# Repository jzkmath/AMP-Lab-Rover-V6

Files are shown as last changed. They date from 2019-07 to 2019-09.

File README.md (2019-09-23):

# AMP-Lab-Rover-V6
Low Cost Rover V6 Design Files.

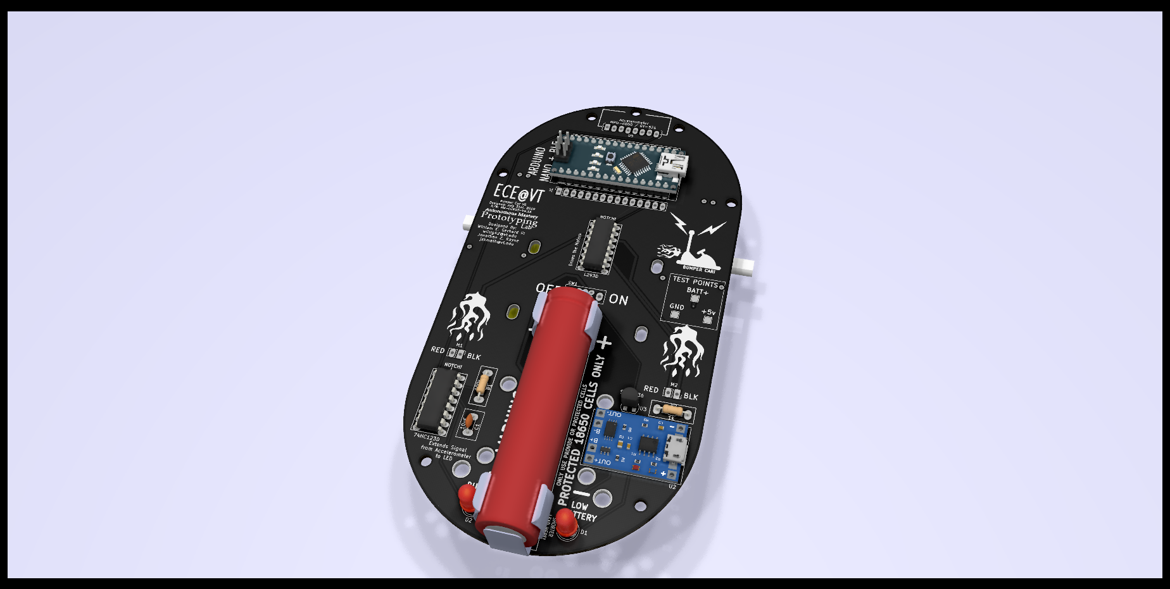
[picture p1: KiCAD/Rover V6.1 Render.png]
render1


This uses a Arduino Nano with Bluetooth Low Energy Module built-in to communicate with a smartphone through the Blynk App.

You will need to download the Blynk library to get the sketch to compile.

## Assembly Instructions

Video Tutorial: https://www.youtube.com/playlist?list=PL4FFrmT3l_b0y4ERLvnKdsL8f40yGXgXS

Written Manual: TBA

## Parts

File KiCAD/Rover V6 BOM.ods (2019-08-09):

Item | Qty | Reference(s) | Description | McMaster Carr PN | Amazon PN | Digikey PN | Link | Unit Cost | Total Cost
1 | 1 | A1 | Arduino Nano + BLE |  | B07QM6KHS4 |  | https://amzn.com/B07QM6KHS4 | $10.99 | $10.99
2 | 2 | BT1 | Battery Clip, Keystone 54 |  |  | 36-54-ND | https://www.digikey.com/short/p9dctd | $0.57 | $1.14
3 | 1 | C1 | 10uF Capacitor |  |  | 445-8396-ND | https://www.digikey.com/short/p9dc35 | $0.40 | $0.40
4 | 1 | D1 | LED |  |  | C5SMF-RJF-CT0W0BB1-ND | https://www.digikey.com/short/p9dc3v | $0.14 | $0.14
5 | 1 | D2 | RGB LED |  | B01C19ENG4 |  | https://amzn.com/B01C19ENG4 | $0.0698 | $0.07
6 | 2 | M1, M2 | Arduino DC Gearbox Motor |  | B07DQGX369 |  | https://amzn.com/B07DQGX369 | $3.75 | $7.50
7 | 1 | R2 | 1k Resistor |  |  | CF18JT1K00CT-ND | https://www.digikey.com/short/p9dcq3 | $0.10 | $0.10
8 | 1 | R1 | 100k Resistor |  |  | CF18JT100KCT-ND | https://www.digikey.com/short/p9dcqn | $0.10 | $0.10
9 | 1 | SW1 | DPDT Switch, EG2207 |  |  | EG1940-ND | https://www.digikey.com/short/pb880n | $0.84 | $0.84
10 | 1 | U1 | L293D Motor Driver IC |  |  | 497-2936-5-ND | https://www.digikey.com/short/p9039w | $3.91 | $3.91
11 | 1 | U2 | TP4056 Charger Module |  | B071RG4YWM |  | https://amzn.com/B071RG4YWM | $0.939 | $0.94
12 | 1 | U4 | S-80836CNY-B2-U Voltage Detector |  |  | 1662-1815-ND | https://www.digikey.com/short/p9dcjj | $0.80 | $0.80
13 | 1 | U5 | 74HC123D IC |  |  | TC74HC123APNEWF-ND | https://www.digikey.com/short/p9dcjd | $0.62 | $0.62
14 | 1 | U6 | MPU-6050 Accelerometer |  | B00LP25V1A |  | https://amzn.com/B00LP25V1A | $3.00 | $3.00
15 | 1 | N/A | 18650 Battery |  |  |  | https://liionwholesale.com/collections/batteries/products/protected-lg-f1l-3350mah-li-ion-18650-button-top-battery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 | $6.50 | $6.50
16 | 1 | N/A | Rear Wheel |  | B00YCE9MIQ |  | https://amzn.com/B00YCE9MIQ | $3.79 | $3.79
17 | 2 | N/A | 8-32 1.5” Screw | 90272A203 |  |  | https://www.mcmaster.com/90272A203 | $0.06 | $0.12
18 | 2 | N/A | 8-32 Standoff | 91780A309 |  |  | https://www.mcmaster.com/91780A309 | $0.37 | $0.74
19 | 2 | N/A | 8-32 Nut | 90480A009 |  |  | https://www.mcmaster.com/90480A009 | $0.02 | $0.04
20 | 4 | N/A | Zipties |  | B075S183BS |  | https://amzn.com/B075S183BS | $0.05 | $0.20
21 | 2 | N/A | DIP16 Socket (optional) |  |  | ED3046-5-ND | https://www.digikey.com/short/p9dc7d | $0.19 | $0.38
22 | 1 | N/A | Custom PCB |  |  |  | https://jlcpcb.com/quote | $2.00 | $2.00
 |  |  | TOTAL COST: |  |  |  |  |  | $44.32

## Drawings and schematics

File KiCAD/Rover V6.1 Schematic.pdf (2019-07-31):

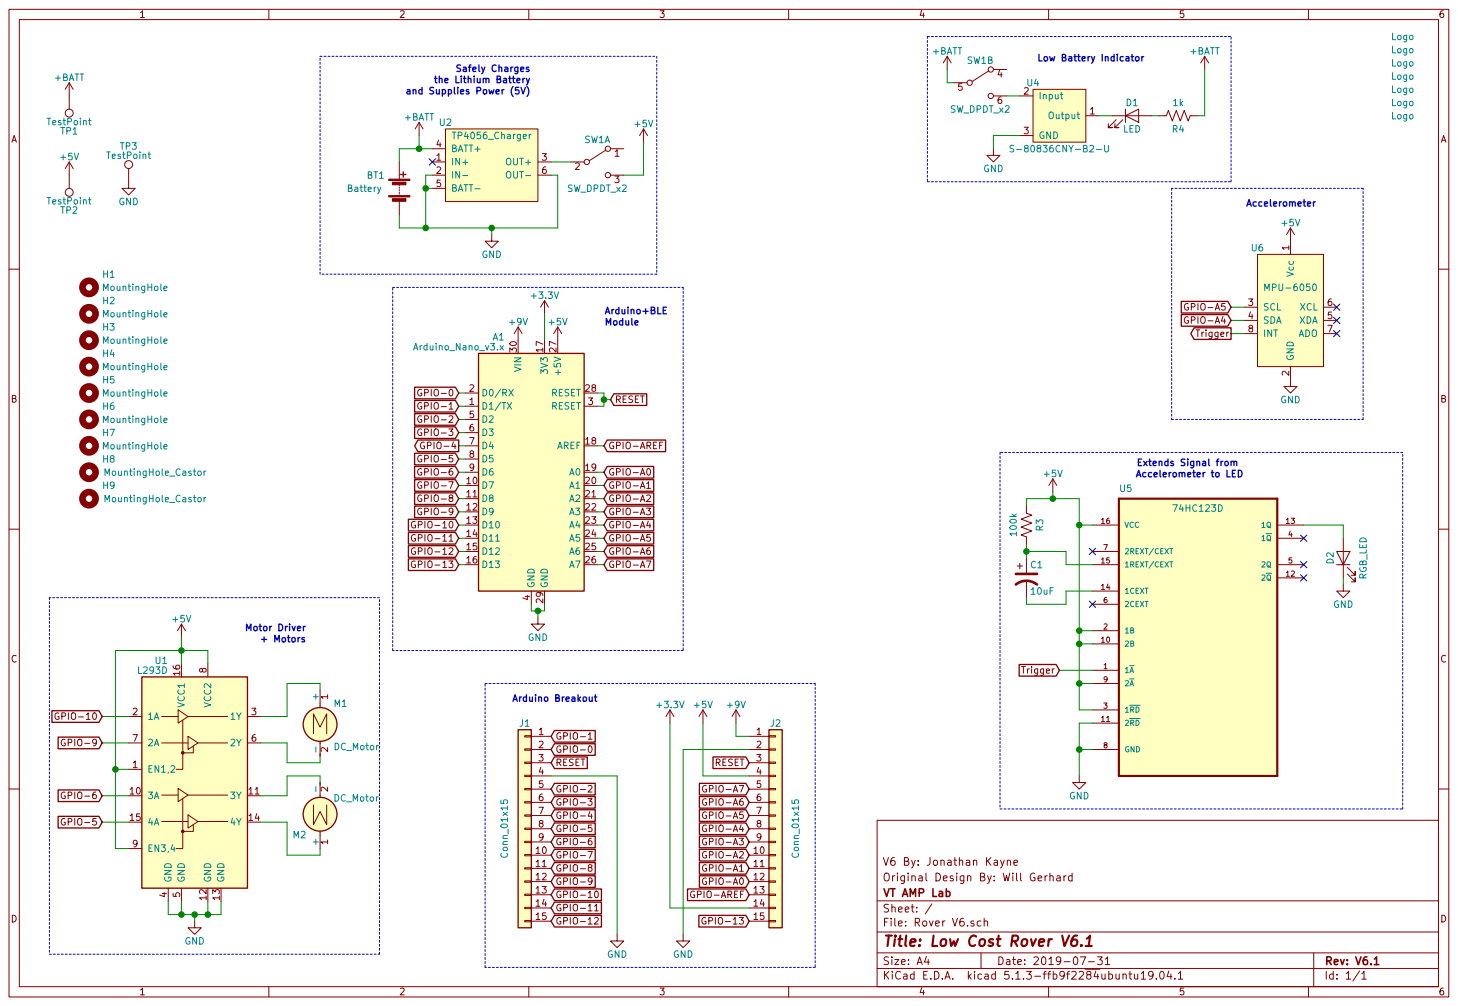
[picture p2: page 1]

2 SCL 3 SDA 4 XDA 5 XCL 6 ADO 7

2A 7 1A 2 EN1,2 1 | VCC2 1Y | 3 GND

V6 By: Jonathan Kayne
File: Rover V6.sch Sheet: / VT AMP Lab Original Design By: Will Gerhard

Id: 1/1 Title: Low Cost Rover V6.1

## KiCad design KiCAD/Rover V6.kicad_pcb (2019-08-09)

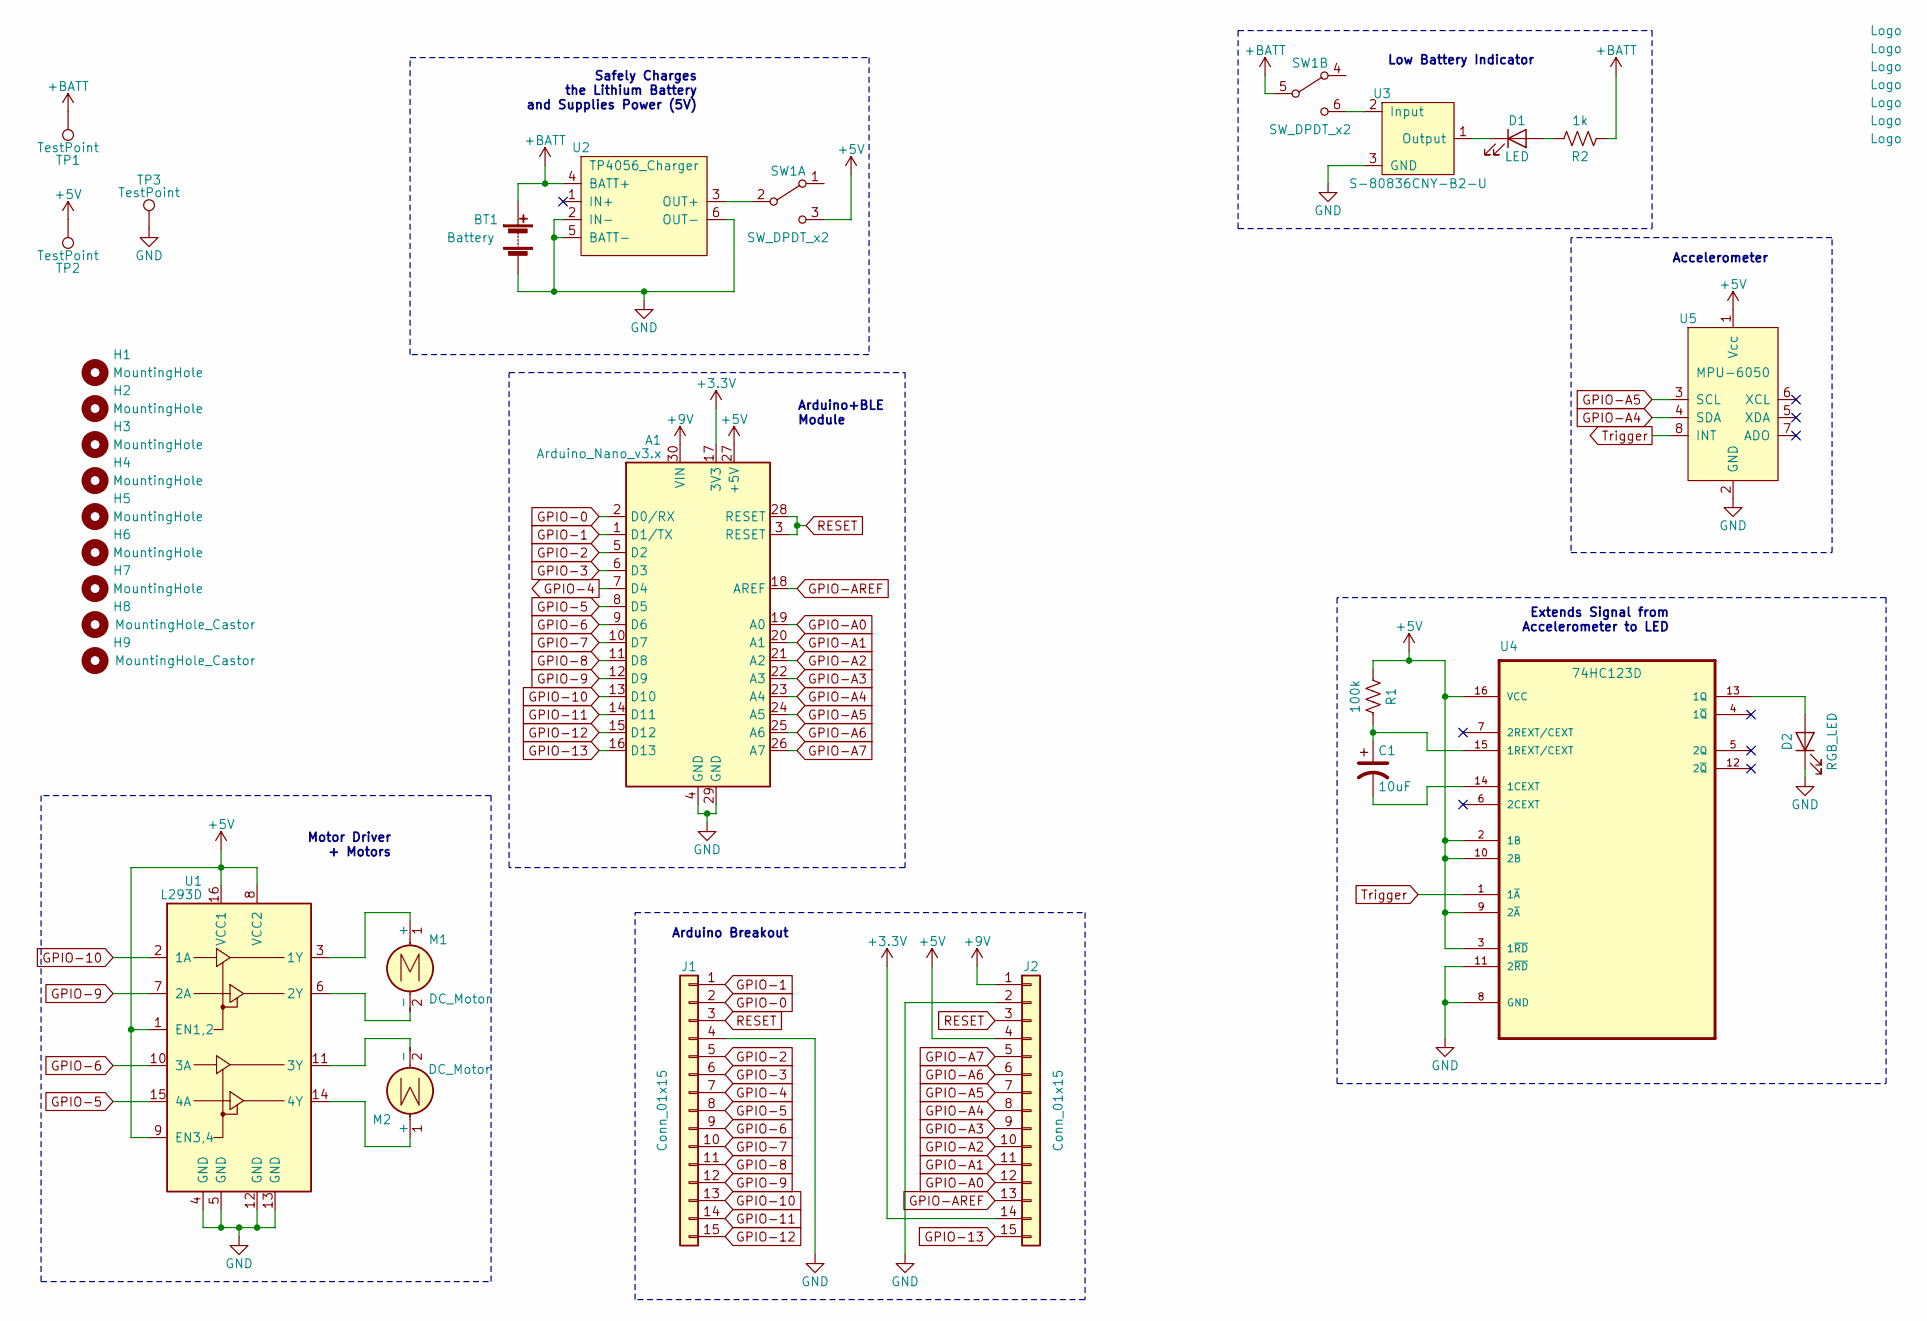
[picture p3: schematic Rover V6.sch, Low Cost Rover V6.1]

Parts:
A1: Arduino_Nano_v3.x; Arduino_Nano_Handsolder
BT1: Battery; 54x2; Digikey PN 36-54-ND
C1: 10uF; C_Disc_D4.3mm_W1.9mm_P5.00mm_Handsolder; Digikey PN 445-8396-ND
D1: LED; LED_D5.0mm_handsolder; Digikey PN C5SMF-RJF-CT0W0BB1-ND
D2: RGB_LED; LED_D5.0mm_handsolder
G1, G2: Logo; bolt
G3: Logo; bumper
G4, G5: Logo; flame
G6: Logo; flame_tiny
G7: Logo; LOGO2
H1, H2, H3, H4, H5, H6, H7: MountingHole; MountingHole_3.2mm_M3
H8: MountingHole_Castor; Ball_Caster
H9: MountingHole_Castor; Castor_Wheel
J1, J2: Conn_01x15; PinSocket_1x15_P2.54mm_Vertical_Handsolder
M1: DC_Motor; Motor
M2: DC_Motor; Motor_Mirror_true
R1: 100k; R_Combo; Digikey PN CF18JT100KCT-ND
R2: 1k; R_Combo; Digikey PN CF18JT1K00CT-ND
SW1: SW_DPDT_x2; Switch-EG2207; Digikey PN EG1940-ND
TP1, TP2, TP3: TestPoint; TestPoint_Pad_2.0x2.0mm
U1: L293D; DIP16_labeled; Digikey PN 497-2936-5-ND
U2: TP4056_Charger; TP4056_Module
U3: S-80836CNY-B2-U; TO-92_HandSolder; Digikey PN 1662-1815-ND
U4: 74HC123D; DIP16_labeled; Digikey PN TC74HC123APNEWF-ND
U5: MPU-6050; PinSocket_1x08_P2.54mm_Vertical_Zigzag

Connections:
+3V3: A1.17 (3V3), J2.14
+5V: A1.27 (+5V), J2.4, R1.1, SW1.3 (C), TP2.1, U1.1 (EN1,2), U1.8 (VCC2), U1.9 (EN3,4), U1.16 (VCC1), U4.2 (1B), U4.3 (1~RD), U4.9 (2~A), U4.10 (2B), U4.16 (VCC), U5.1 (Vcc)
+9V: A1.30 (VIN), J2.1
+BATT: BT1.1 (+), R2.1, SW1.5 (B), TP1.1, U2.4 (BATT+)
GND: A1.4 (GND), A1.29 (GND), BT1.2 (-), D2.1 (K), J1.4, J2.2, TP3.1, U1.4 (GND), U1.5 (GND), U1.12 (GND), U1.13 (GND), U2.2 (IN-), U2.5 (BATT-), U2.6 (OUT-), U3.3 (GND), U4.8 (GND), U4.11 (2~RD), U5.2 (GND)
GPIO-0: A1.2 (D0/RX), J1.2
GPIO-1: A1.1 (D1/TX), J1.1
GPIO-2: A1.5 (D2), J1.5
GPIO-3: A1.6 (D3), J1.6
GPIO-4: A1.7 (D4), J1.7
GPIO-5: A1.8 (D5), J1.8, U1.15 (4A)
GPIO-6: A1.9 (D6), J1.9, U1.10 (3A)
GPIO-7: A1.10 (D7), J1.10
GPIO-8: A1.11 (D8), J1.11
GPIO-9: A1.12 (D9), J1.12, U1.7 (2A)
GPIO-10: A1.13 (D10), J1.13, U1.2 (1A)
GPIO-11: A1.14 (D11), J1.14
GPIO-12: A1.15 (D12), J1.15
GPIO-13: A1.16 (D13), J2.15
GPIO-A0: A1.19 (A0), J2.12
GPIO-A1: A1.20 (A1), J2.11
GPIO-A2: A1.21 (A2), J2.10
GPIO-A3: A1.22 (A3), J2.9
GPIO-A4: A1.23 (A4), J2.8, U5.4 (SDA)
GPIO-A5: A1.24 (A5), J2.7, U5.3 (SCL)
GPIO-A6: A1.25 (A6), J2.6
GPIO-A7: A1.26 (A7), J2.5
GPIO-AREF: A1.18 (AREF), J2.13
unnamed: C1.1, R1.2, U4.15 (1REXT/CEXT)
unnamed: C1.2, U4.14 (1CEXT)
unnamed: D1.1 (K), U3.1 (Output)
unnamed: D1.2 (A), R2.2
unnamed: D2.2 (A), U4.13 (1Q)
unnamed: M1.1 (+), U1.3 (1Y)
unnamed: M1.2 (-), U1.6 (2Y)
unnamed: M2.1 (+), U1.14 (4Y)
unnamed: M2.2 (-), U1.11 (3Y)
unnamed: SW1.2 (B), U2.3 (OUT+)
unnamed: SW1.6 (C), U3.2 (Input)
RESET: A1.3 (RESET), A1.28 (RESET), J1.3, J2.3
Trigger: U4.1 (1~A), U5.8 (INT)

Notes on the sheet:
Low Battery Indicator
Accelerometer
Extends Signal from Accelerometer to LED
Motor Driver + Motors
Safely Charges the Lithium Battery and Supplies Power (5V)
Arduino+BLE Module
Arduino Breakout

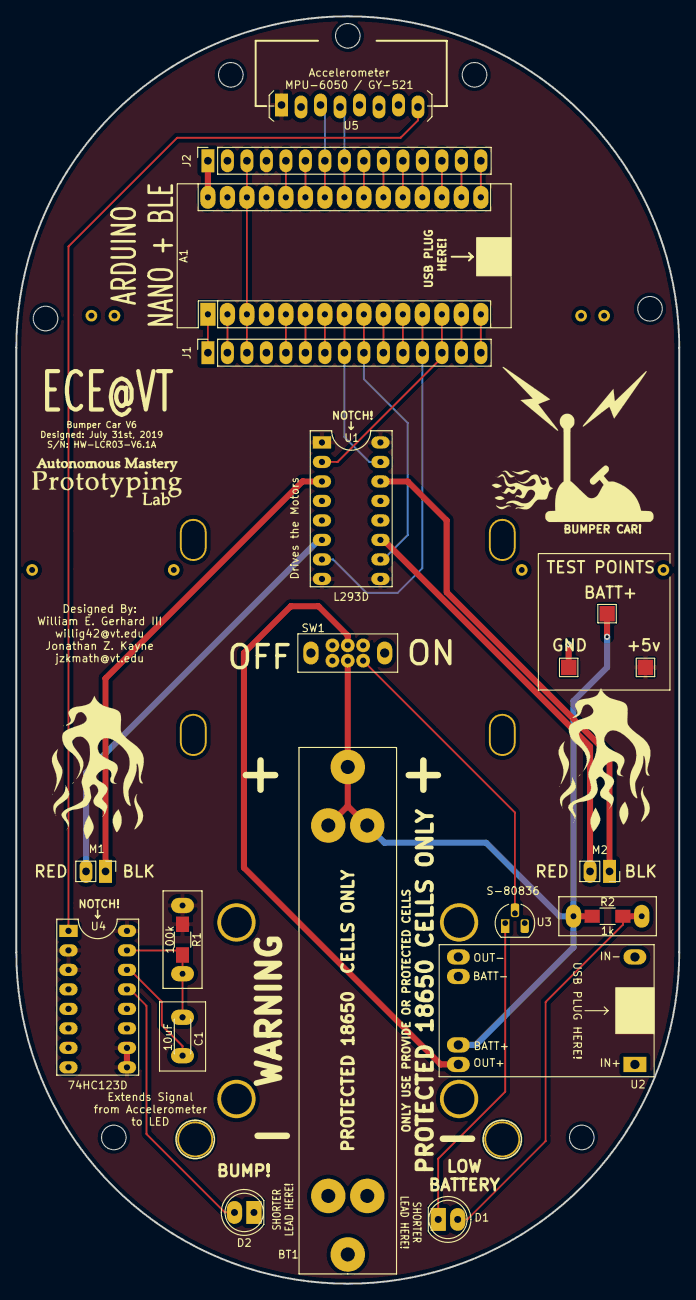
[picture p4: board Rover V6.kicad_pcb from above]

Board: 2 copper layers, 86.4 x 165.1 mm, 36 parts (0 on the bottom side), 41 nets.

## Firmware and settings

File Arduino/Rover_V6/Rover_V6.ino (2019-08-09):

/*************************************************************
  LOW COST ROVER V6 - ARDUINO CODE
  By: Jonathan Kayne, Virginia Tech ECE Class of 2021
  jzkmath@vt.edu
  Based off the Low Cost Rover By Will Gerhard

  Uses the Arduino BLE-Nano board from eMakeFun to communicate with
  a smartphone via Bluetooth Low Energy (BLE, or Bluetooth 4.0).
  This requires the use of an App called Blynk (by Sparkfun)
  which is available on iOS and Android.

  Make sure to edit the auth token below so that the
  rover is unique!

  Also, use the setup sketch to configure your device!
   
  Download latest Blynk library here:
    https://github.com/blynkkk/blynk-library/releases/latest

  Blynk is a platform with iOS and Android apps to control
  Arduino, Raspberry Pi and the likes over the Internet.
  You can easily build graphic interfaces for all your
  projects by simply dragging and dropping widgets.

    Downloads, docs, tutorials: http://www.blynk.cc

  Blynk library is licensed under MIT license

 *************************************************************

  You can receive x and y coords for joystick movement within App.

  App project setup:
    HARDWARE MODEL: Arduino Nano
    CONNECTION TYPE: BLE
    
    - BLE widget
    - Two Axis Joystick on V1 in MERGE output mode.
    - Range set from -127 to 127 for both x and y.
   
 *************************************************************/
 
#include <BlynkSimpleSerialBLE.h>
#include <Wire.h>

// ***************************************************
// You should get Auth Token in the Blynk App.
// Go to the Project Settings (nut icon).
char auth[] = "YourAuthToken";

// Max speed for the rover.
// any value between 0 and 255 is acceptable.
// only adjust if you want to make the rover slower!
#define MAX_SPEED 255

// ***************************************************

// Arduino Motor Pins
#define R_MOT_F 5
#define R_MOT_R 6
#define L_MOT_F 10
#define L_MOT_R 9

void setup()
{
  // Pin initialization
  pinMode(LED_BUILTIN, OUTPUT);
  pinMode(R_MOT_F, OUTPUT);
  pinMode(R_MOT_R, OUTPUT);
  pinMode(L_MOT_F, OUTPUT);
  pinMode(L_MOT_R, OUTPUT);
  
  // set up serial and change device name
  Serial.begin(9600);
  delay(1000);
  initAccelerometer();
  delay(1000);

  // start up Blynk
  Blynk.begin(Serial, auth);
}

void loop()
{
  Blynk.run();
}


// ***************************************************
// MOTOR DRIVER
// This function takes the Joystick values from Blynk
// and runs the motors based on the coordinates.
// This was ultimately ported from Will's Python code
// that was used on the Onion Omegas in previous versions.
// It seems a bit complex, because it has differential steering (like a tank)
// ***************************************************
BLYNK_WRITE(V1) 
{
  // get the Joystick coordinates from Blynk
  int nJoyX = param[0].asInt();
  int nJoyY = param[1].asInt();

  // set some varaibles
  int fPivYLimit = 32;
  int fPivScale = 0;
  int nMotPremixL = 0;
  int nMotPremixR = 0;
  
  // Calculate Drive Turn output due to Joystick X input
  if (nJoyY >= 0) // *** FORWARD ***
  {
    if (nJoyX >= 0) 
    {
      // Right
      nMotPremixL = 127;
      nMotPremixR = (127 - nJoyX);
    }
    else 
    {
      // Left
      nMotPremixL = (127 + nJoyX);
      nMotPremixR = 127;
    }
  }
  else // *** REVERSE ***
  {
    if (nJoyX >= 0) 
    {
      // Right
      nMotPremixL = (127 - nJoyX);
      nMotPremixR = 127;
    }
    else 
    {
      // Left
      nMotPremixL = 127;
      nMotPremixR = (127 + nJoyX);
    }
  }

  // Scale Drive output due to Joystick Y input (throttle)
  nMotPremixL = nMotPremixL * nJoyY/128;
  nMotPremixR = nMotPremixR * nJoyY/128;

  // Now calculate pivot amount
  // pivot strength (nPivSpeed) is based on Joystick X
  // pivot and drive blending (fPivScale) is based on Joystick Y
  int nPivSpeed = nJoyX;
  if (abs(nJoyY) > fPivYLimit)
  {
    fPivScale = 0;
  }
  else
  {
    fPivScale = (1 - abs(nJoyY)/fPivYLimit);
  }

  // Calculate final mix of drive and pivot
  int nMotMixL = (1 - fPivScale)*nMotPremixL + fPivScale*(nPivSpeed);
  int nMotMixR = (1 - fPivScale)*nMotPremixR + fPivScale*((-1)*nPivSpeed);

  // Scale the values
  int Rg = map(nMotMixL, -127, 127, ((-1)*MAX_SPEED), MAX_SPEED);
  int Lg = map(nMotMixR, -127, 127, ((-1)*MAX_SPEED), MAX_SPEED);

  // Now, we can set the motor speeds based on Rg and Lg
  if ((Rg == 0) && (Lg == 0)) // *** STOPPED ***
  {
    digitalWrite(R_MOT_F, LOW);
    digitalWrite(R_MOT_R, LOW);
    digitalWrite(L_MOT_F, LOW);
    digitalWrite(L_MOT_R, LOW);
  }
  else if ((Rg < -250) && (Lg < -250)) // *** FULL SOUTH *** 
  {
    digitalWrite(R_MOT_F, HIGH);
    digitalWrite(R_MOT_R, LOW);
    digitalWrite(L_MOT_F, HIGH);
    digitalWrite(L_MOT_R, LOW);
  }
  else if ((Rg < -250) && (Lg < 0)) // *** SOUTHWEST *** 
  {
    digitalWrite(R_MOT_F, HIGH);
    digitalWrite(R_MOT_R, LOW);
    analogWrite(L_MOT_F, abs(Lg));
    digitalWrite(L_MOT_R, LOW);
  }
  else if ((Rg < 0) && (Lg < -250)) // *** SOUTHEAST *** 
  {
    analogWrite(R_MOT_F, abs(Rg));
    digitalWrite(R_MOT_R, LOW);
    digitalWrite(L_MOT_F, HIGH);
    digitalWrite(L_MOT_R, LOW);
  }
  else if ((Rg < 0) && (Lg < 0)) // *** SOUTH *** 
  {
    analogWrite(R_MOT_F, abs(Rg));
    digitalWrite(R_MOT_R, LOW);
    analogWrite(L_MOT_F, abs(Lg));
    digitalWrite(L_MOT_R, LOW);
  }
  else if ((Rg > 250) && (Lg < 0)) // *** FULL EAST *** 
  {
    digitalWrite(R_MOT_R, LOW);
    digitalWrite(R_MOT_F, HIGH);
    analogWrite(L_MOT_R, abs(Lg));
    digitalWrite(L_MOT_F, LOW);
  }
  else if ((Rg > 0) && (Lg < 0)) // *** EAST *** 
  {
    digitalWrite(R_MOT_R, LOW);
    analogWrite(R_MOT_F, Rg);
    analogWrite(L_MOT_R, abs(Lg));
    digitalWrite(L_MOT_F, LOW);
  }
  else if ((Rg < 0) && (Lg > 250)) // *** FULL WEST *** 
  {
    analogWrite(R_MOT_R, abs(Rg));
    digitalWrite(R_MOT_F, LOW);
    digitalWrite(L_MOT_R, LOW);
    digitalWrite(L_MOT_F, HIGH);
  }
  else if ((Rg < 0) && (Lg > 0)) // *** WEST *** 
  {
    analogWrite(R_MOT_R, abs(Rg));
    digitalWrite(R_MOT_F, LOW);
    digitalWrite(L_MOT_R, LOW);
    analogWrite(L_MOT_F, Lg);
  }
  else if ((Rg > 250) && (Lg > 250)) // *** FULL NORTH *** 
  {
    digitalWrite(R_MOT_F, HIGH);
    digitalWrite(R_MOT_R, LOW);
    digitalWrite(L_MOT_F, LOW);
    digitalWrite(L_MOT_R, HIGH);
  }
  else // *** NORTH ***
  {
    digitalWrite(R_MOT_F, LOW);
    analogWrite(R_MOT_R, Lg);
    digitalWrite(L_MOT_F, LOW);
    analogWrite(L_MOT_R, Rg);
  }
  
}



// ***************************************************
// Initializes the MPU-6050 / GY-521 Accelerometer.
// This is done by sending I2C commands so that when a bump is detected,
// a pulse will be sent to the 74HC123D via the interrupt pin.
// ***************************************************
void initAccelerometer()
{
  Wire.begin();
  
  Wire.beginTransmission(0x68);
  Wire.write(0x6B);
  Wire.write(0x00);
  Wire.endTransmission();

  Wire.beginTransmission(0x68);
  Wire.write(0x68);
  Wire.write(0x07);
  Wire.endTransmission();

  Wire.beginTransmission(0x68);
  Wire.write(0x37);
  Wire.write(0x82);
  Wire.endTransmission();

  Wire.beginTransmission(0x68);
  Wire.write(0x1C);
  Wire.write(0x01);
  Wire.endTransmission();

  Wire.beginTransmission(0x68);
  Wire.write(0x1F);
  Wire.write(0x1A);
  Wire.endTransmission();

  Wire.beginTransmission(0x68);
  Wire.write(0x20);
  Wire.write(0x05);
  Wire.endTransmission();

  Wire.beginTransmission(0x68);
  Wire.write(0x69);
  Wire.write(0x15);
  Wire.endTransmission();

  Wire.beginTransmission(0x68);
  Wire.write(0x38);
  Wire.write(0x40);
  Wire.endTransmission();
}

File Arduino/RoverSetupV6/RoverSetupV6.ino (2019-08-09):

/*
 * ROVER SETUP
 * By: Jonathan Kayne, Virginia Tech ECE 2019
 * 
 * This program allows you to configure the BLE+Nano board so that it works.
 * Upload this code to the board, then open a serial monitor
 * (Tools > Serial Monitor, or CTRL+Shift+M)
 * and set the monitor to "Both NL and CR" at 9600 baud.
 * 
 * Set up the board by typing in the given commands to name the device and allow for communication.
 */


byte comdata;

void setup()
 {
     Serial.begin(9600);
     Serial.println("BLE Test");
     Serial.println("Put in AT+NAME=First-Last to set up your name.");
     Serial.println("Next, type AT+PASS=123456");
     Serial.println("Next, type AT+AUTH=0");
     Serial.println("Next, type AT+BLEUSB=3");
 }

void loop()
 {
     while (Serial.available() > 0)  
     {
         comdata = Serial.read();
         delay(2);
         Serial.write(comdata);
     }
 }

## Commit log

2019-07-31 Adding KiCAD files
2019-07-31 Adding KiCAD files again
    [Rover V6 BOM.ods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]
2019-08-09 Updated Arduino
    [Rover V6 BOM.ods, Rover V6 BOM.xlsx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]
